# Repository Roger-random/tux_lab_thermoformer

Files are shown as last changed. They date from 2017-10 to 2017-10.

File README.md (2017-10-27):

# Tux-Lab Thermoforming Machine project

Files related to getting the Tux-Lab thermoforming machine back up and running.

## controls/AcrylicRelayPanel

Files for laser-cutting the relay panel and the toggle switches panel

## pi_touch_ui

The initial goal is to get the machine up and running with manual toggle switches. But being the tinkerer type - we know we will want to do more. This respository starts with an effort to create a machine control UI with PyQt5. The idea is to mount a Raspberry Pi the machine and control the machine this way.

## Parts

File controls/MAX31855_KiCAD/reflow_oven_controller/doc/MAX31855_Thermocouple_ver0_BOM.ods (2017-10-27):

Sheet: cc3300 V1
cc3000 WiFi Module
 |  |  |  |  |  |  |  |  | Buy
Quantity | Component | Part | Vendor | Vendor Item Number | Manufacturer | Manuf Part No. | Note | Cost | Qty | Price | Ext Price | Link
1 | C1 | 2.2pF 0603 | Digikey | 445-5617-1-ND | TDK | CGA3E2C0G1H2R2C080AA | CAP CER 2.2PF 50V NP0 0603 | 0.1 | 100 | 0.033 | 3.300 | http://www.digikey.com/product-detail/en/CGA3E2C0G1H2R2C080AA/445-5617-1-ND/2443657
1 | C2 | 10pF 0603 | Digikey | 445-1269-1-ND | TDK | C1608C0G1H100D080AA | CAP CER 10PF 50V NP0 0603 | 0.1 | 100 | 0.017 | 1.650 | http://www.digikey.com/product-detail/en/C1608C0G1H100D080AA/445-1269-1-ND/567671
1 | C3 | 1uF 0603 | Digikey
1 | C4 | 1uF 0603 | Digikey
1 | L1 | n/a | Digikey
1 | L2 | 2.2nH 0603 | Digikey | 712-1427-1-ND | Johnson Tech | L-14C2N2SV4T | CER INDUCTOR 2.2NH 0603 | 0.10 | 50 | 0.046 | 2.320 | http://www.digikey.com/product-detail/en/L-14C2N2SV4T/712-1427-1-ND/1914877
1 | U1 | TI cc3000 wifi | Digikey | 296-35057-ND | TI | CC3000MOD | MOD SIMPLELINK WI-FI CC300 | 14.49 | 3 | 14.490 | 43.470 | http://www.digikey.com/product-detail/en/CC3000MOD/296-35057-ND/3725883
1 | U2 | 74HC4050 | Digikey | 296-9215-1-ND | TI | CD74HC4050PWR | IC BUFFER HEX 1INPUT 16TSSOP | 0.49 | 10 | 0.412 | 4.120 | http://www.digikey.com/product-detail/en/CD74HC4050PWR/296-9215-1-ND/376723
1 | K1 | 3 pin header | Digikey
1 | K2 | 3 pin header | Digikey
1 | P1 | 7 pin header | Digikey
1 | Antenna | Antenna for FCC comp | Digikey | 712-1403-1-ND | Johnson Tech | 2500AT44M0400E | ANTENNA CHIP UWB 2.3 - 2.7 GHZ | 1.35 | 10 | 1.128 | 11.280 | http://www.digikey.com/product-detail/en/2500AT44M0400E/712-1403-1-ND/1840081
 |  |  |  |  |  |  | Component Cost: | 15.28 |  | 14.998 | 54.860

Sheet: MPL3115A2
MPL3115A2 WiFi Module
 |  |  |  |  |  |  |  |  | Buy
Quantity | Component | Part | Vendor | Vendor Item Number | Manufacturer | Manuf Part No. | Note | Cost | Qty | Price | Ext Price | Link
1* | C1 | 100nF | Digikey | 399-1095-1-ND | Kemet | C0603C104K8RACTU | 10V instead of 6.3V | 0.1 | 250 | 0.00944 |  | http://www.digikey.com/product-detail/en/C0603C104K8RACTU/399-1095-1-ND/411370
1* | C2 | 10uF | Digikey | 445-9104-1-ND | TDK | C1608X7S0J106M080AC | CAP CER 10UF 6.3V 20% X7S 0603 | 0.53 | 10 | 0.503 |  | http://www.digikey.com/product-detail/en/C1608X7S0J106M080AC/445-9104-1-ND/3661624
1* | C3 | 100nF | Digikey | 399-1095-1-ND | Kemet | C0603C104K8RACTU | 10V instead of 6.3V | 0.1 | 250 | 0.00944 |  | http://www.digikey.com/product-detail/en/C0603C104K8RACTU/399-1095-1-ND/411370
1* | C4 | .1uF | Digikey | 445-1314-1-ND | TDK | C1608X7R1H104K080AA | CAP CER 0.1UF 50V 10% X7R 0603 | 0.1 | 250 | 0.018 |  | http://www.digikey.com/product-detail/en/C1608X7R1H104K080AA/445-1314-1-ND/567687
1 | Q1 | BSS138 | Digikey | BSS138CT-ND | Fairchild | BSS138 | MOSFET N-CH 50V 220MA SOT-23 | 0.22 | 25 | 0.141 | 3.520 | http://www.digikey.com/product-detail/en/BSS138/BSS138CT-ND/244294
1 | Q2 | BSS138 | Digikey | BSS138CT-ND | Fairchild | BSS138 | MOSFET N-CH 50V 220MA SOT-23 | 0.22 | 25 | 0.141 | 3.520 | http://www.digikey.com/product-detail/en/BSS138/BSS138CT-ND/244294
1* | R1 | 10K | Digikey | MCT0603-10.0K-CFCT-ND | Vishay | MCT06030C1002FP500 | RES 10.0K OHM 1/8W 1% SMD 0603 | 0.08 | 100 | 0.0408 |  | http://www.digikey.com/product-detail/en/MCT06030C1002FP500/MCT0603-10.0K-CFCT-ND/2607933
1* | R2 | 10K | Digikey | MCT0603-10.0K-CFCT-ND | Vishay | MCT06030C1002FP500 | RES 10.0K OHM 1/8W 1% SMD 0603 | 0.08 | 100 | 0.0408 |  | http://www.digikey.com/product-detail/en/MCT06030C1002FP500/MCT0603-10.0K-CFCT-ND/2607933
1* | R3 | 10K | Digikey | MCT0603-10.0K-CFCT-ND | Vishay | MCT06030C1002FP500 | RES 10.0K OHM 1/8W 1% SMD 0603 | 0.08 | 100 | 0.0408 |  | http://www.digikey.com/product-detail/en/MCT06030C1002FP500/MCT0603-10.0K-CFCT-ND/2607933
1* | R4 | 10K | Digikey | MCT0603-10.0K-CFCT-ND | Vishay | MCT06030C1002FP500 | RES 10.0K OHM 1/8W 1% SMD 0603 | 0.08 | 100 | 0.0408 |  | http://www.digikey.com/product-detail/en/MCT06030C1002FP500/MCT0603-10.0K-CFCT-ND/2607933
1 | P1 | 7 Pin Header | Digikey
1 | U1 | MPL3115A2 | Digikey | MPL3115A2-ND | Freescale | MPL3115A2 | IC ALTIMETER I2C VERSION 8LGA | 2.88 | 5 | 2.720 | 13.600 | http://www.digikey.com/product-detail/en/MPL3115A2/MPL3115A2-ND/2817529
 |  |  |  |  |  |  | Component Cost: | 1.59 |  | 3.705 | 20.640
1* | L6470_v1
 | For version 2, go with 0805 C2 to lower cost
 | C2 | 10uF | Digikey | 587-2396-1-ND | Taiyo Yuden | JMK212B7106KG-T | CAP CER 10UF 6.3V 10% X7R 0805 | 0.27 | 50 | 0.111 |  | http://www.digikey.com/product-detail/en/JMK212B7106KG-T/587-2396-1-ND/2179009

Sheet: Si7021
 | MAX31855 Thermocouple Amplifier
 |  |  |  |  |  |  |  |  |  | Buy
 | Quantity | Component | Part | Vendor | Vendor Item Number | Manufacturer | Manuf Part No. | Note | Cost | Qty | Price | Ext Price | Link
 | 4 | C1, C2, C4, C5 | n/a
 | 4 | C3, C6 | .01uF +/-10% 16V X7R 0603 | Digikey | 478-6208-1-ND | AVX Corp | 0603YC103JAT2A | CAP CER 10000PF 16V 5% X7R 0603 | 0.15 | 100 | 0.048 | 4.75 | http://www.digikey.com/product-detail/en/0603YC103JAT2A/478-6208-1-ND/2391407
* | 2 | C7, C8, C9, C10 | 0.1uF +/-10%, 16V X7R 0603 | Digikey | 445-1314-1-ND | TDK | C1608X7R1H104K080AA | CAP CER 0.1UF 50V 10% X7R 0603 | 0.10 | 250 | 0.018 | 4.50 | http://www.digikey.com/product-detail/en/C1608X7R1H104K080AA/445-1314-1-ND/567687
 | 4 | R1, R2, R3, R4 | 150 Ohm +/-5% resistors (0603) | Digikey | MCT0603-150-CFCT-ND | Vishay Beyschlag | MCT06030C1500FP500 | RES 150 OHM 1/8W 1% SMD 0603 | 0.08 | 100 | 0.0408 | 4.08 | http://www.digikey.com/product-detail/en/MCT06030C1500FP500/MCT0603-150-CFCT-ND/2607884
 | 4 | FB1, FB2, FB3, FB4 | 470I ferrite beads (0603) | Digikey | 490-5223-1-ND | Murata | BLM18PG471SN1D | FERRITE CHIP 470 OHM 1000MA 0603 | 0.10 | 100 | 0.0501 | 5.01 | http://www.digikey.com/product-detail/en/BLM18PG471SN1D/490-5223-1-ND/1948399
 | 2 | U1, U2 | TVS diode NUP2105TL1G | Digikey | NUP2105LT1GOSCT-ND | On Semi | NUP2105LT1G | TVS DIODE 24VWM 44VC SOT23 | 0.44 | 10 | 0.37 | 3.71 | http://www.digikey.com/product-detail/en/NUP2105LT1G/NUP2105LT1GOSCT-ND/1485001
 | 2 | Alt U3, U4 | MAX31855KASA+ | Digikey | MAX31855KASA+TCT-ND | Maxim | MAX31855KASA+T | IC CONV THERMOCOUPLE-DGTL 8SOIC | 7.19 | 5 | 7.190 | 35.95 | http://www.digikey.com/product-detail/en/MAX31855KASA%2BT/MAX31855KASA%2BTCT-ND/2708805
 | 1 | U5 | TXB0104 Bidirection Shifter | Digikey | 296-21929-1-ND | TI | TXB0104PWR | IC VOLT-LEVEL TRANSLATOR 14TSSOP | 1.69 | 10 | 1.493 | 14.93 | http://www.digikey.com/product-detail/en/TXB0104PWR/296-21929-1-ND/1629282
** | 2 | P1, P2 | 3.5mm Tblock | Digikey | ED2635-ND | OnShore | OSTTE020161 | TERM BLOCK 3.5MM VERT 2POS PCB | 0.44 | 50 | 0.306 | 15.30 | http://www.digikey.com/product-search/en?vendor=0&keywords=ED2635-ND
 | 1 | P3 | Angle Header | Digikey | WM50026-35-ND | Molex | 22288353 | CONN HEADER 35POS .100 R/A GOLD | 2.07 | 10 | 1.853 | 18.53 | http://www.digikey.com/product-detail/en/0022288353/WM50026-35-ND/314240
 |  |  |  |  |  |  |  | Component Cost: | 19.833 |  | 18.249 | 106.760
 | * | L6470, C10, C11, C12, C13
 | **
 | Digikey Out of Stock – ETA 9/29/14
 | 2 | U3, U4 | MAX31855KASA+ | Digikey | MAX31855KASA+TCT-ND | Maxim | MAX31855KASA+-ND | IC CONV THERMOCOUPLE-DGTL SOIC | 4.50 | 10 | 4.275 | 42.75 | http://www.digikey.com/product-detail/en/MAX31855KASA%2BT/MAX31855KASA%2BTCT-ND/2708805

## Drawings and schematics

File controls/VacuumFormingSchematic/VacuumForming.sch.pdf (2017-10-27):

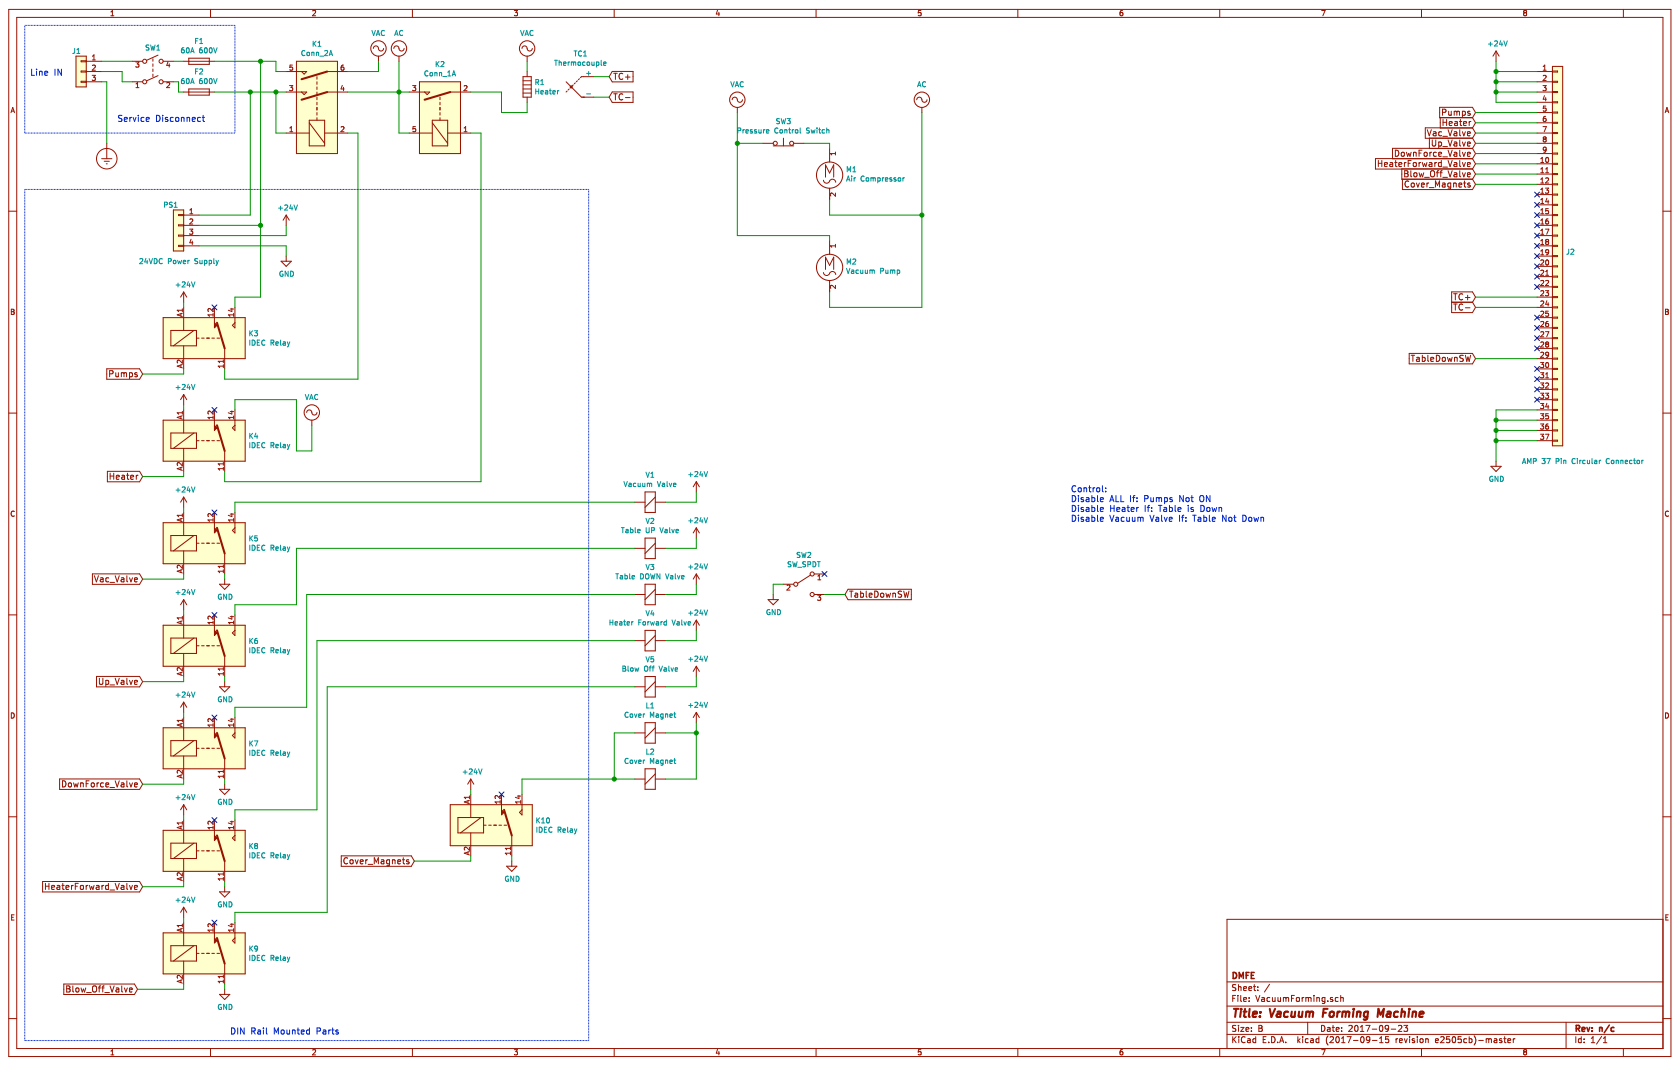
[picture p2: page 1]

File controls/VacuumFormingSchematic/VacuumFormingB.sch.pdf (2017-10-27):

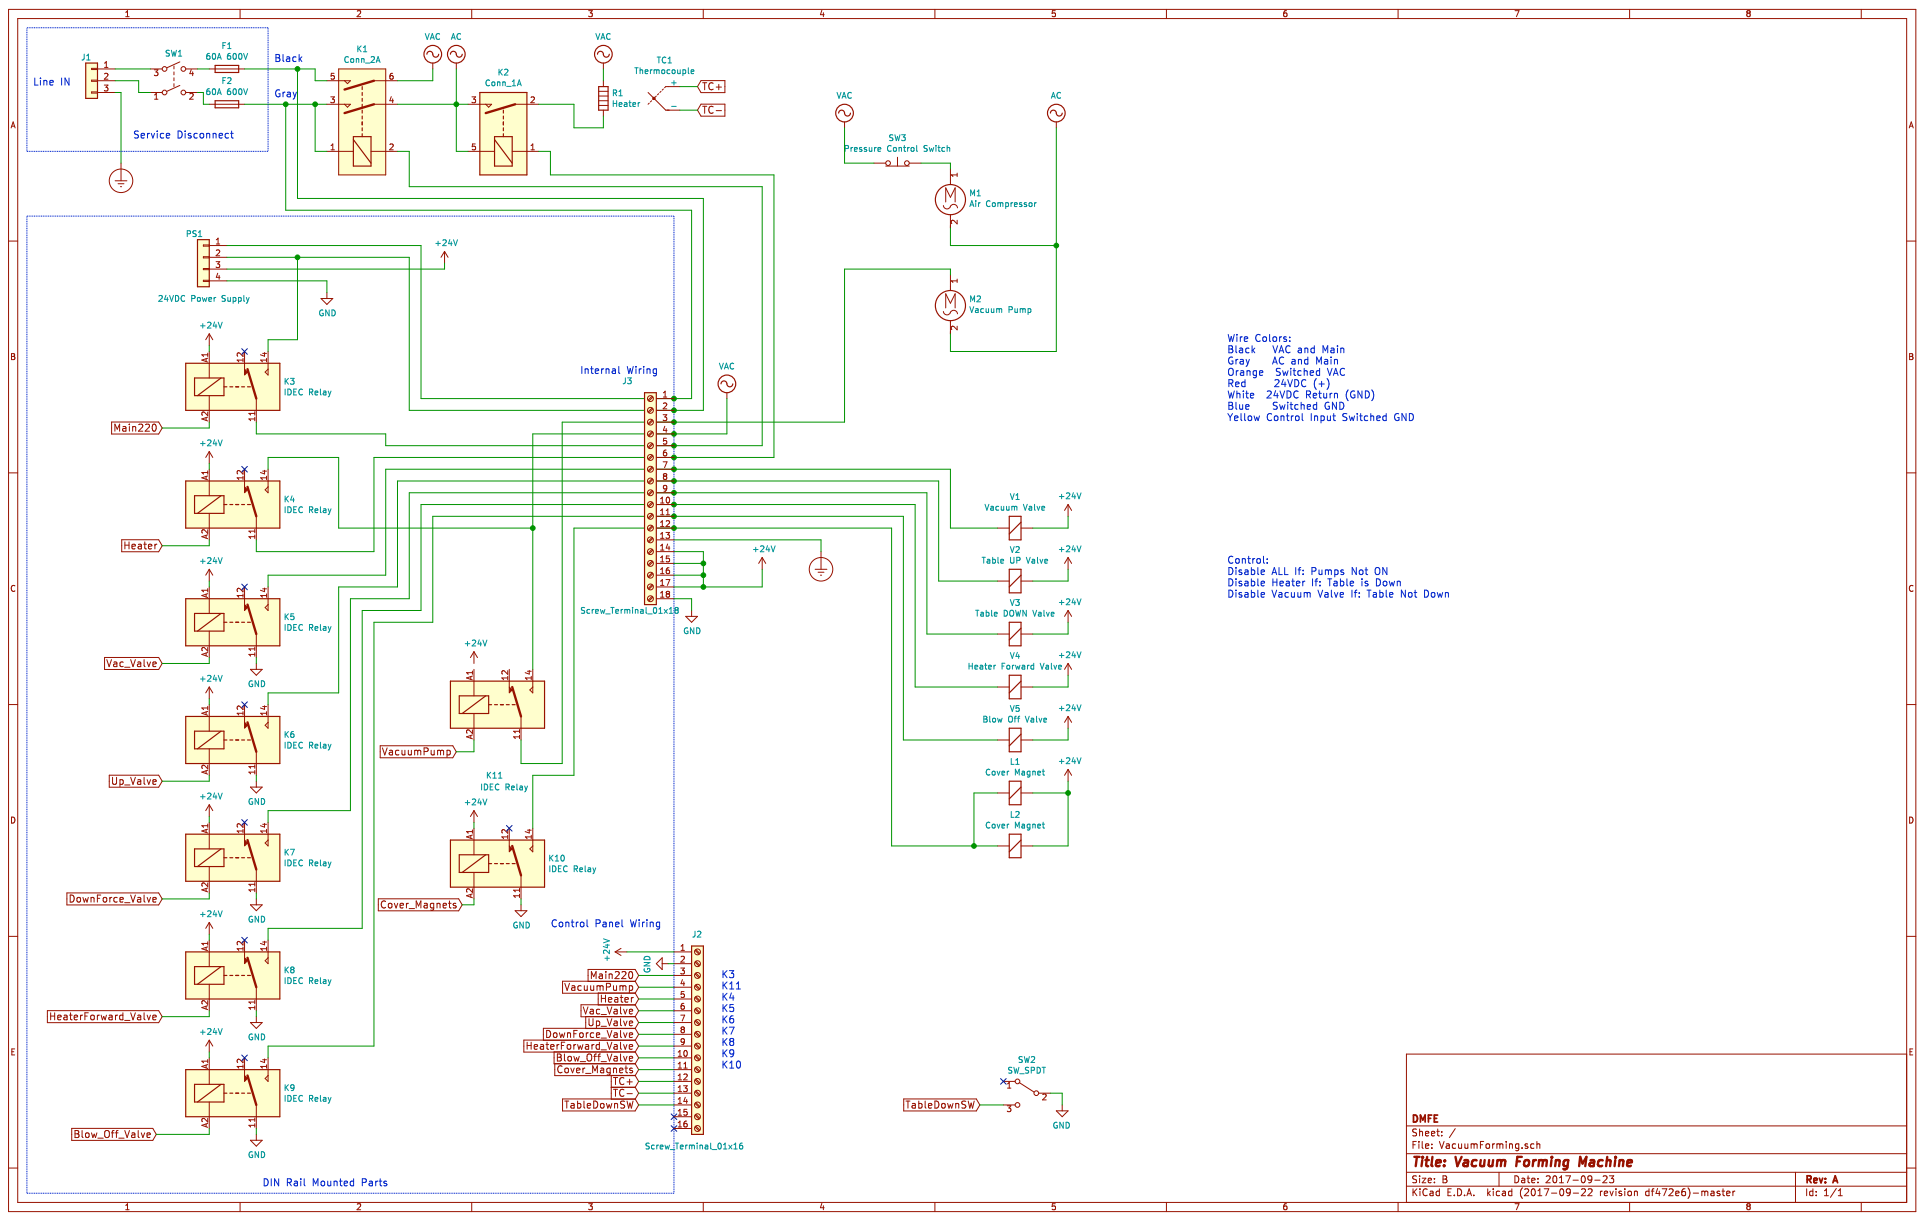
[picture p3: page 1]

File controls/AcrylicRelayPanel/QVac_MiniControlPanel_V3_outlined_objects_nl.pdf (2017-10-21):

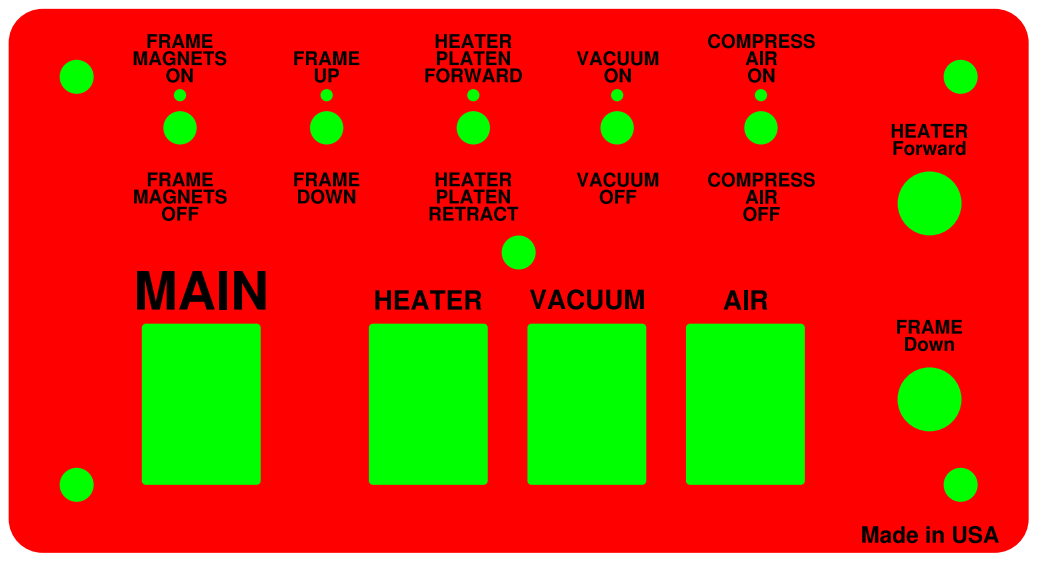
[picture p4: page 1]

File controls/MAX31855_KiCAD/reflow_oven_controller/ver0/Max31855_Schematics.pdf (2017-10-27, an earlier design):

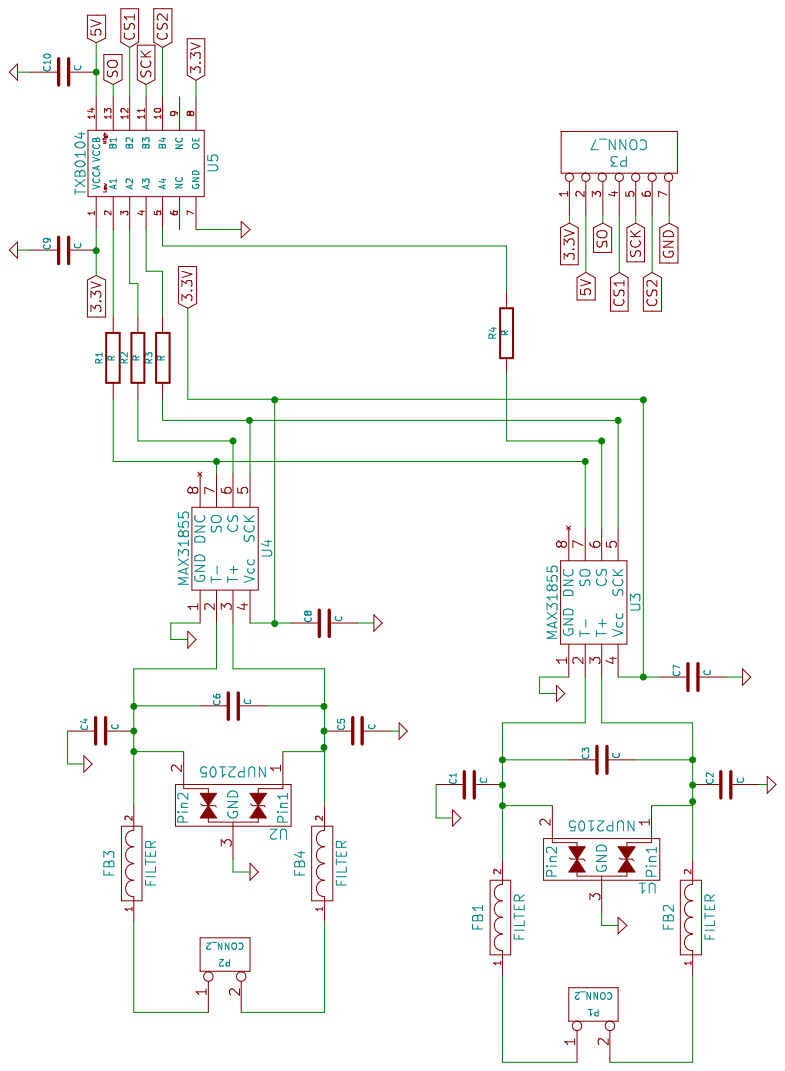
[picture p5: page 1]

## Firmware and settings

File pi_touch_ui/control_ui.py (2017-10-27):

import sys
import threading
from PyQt5.QtCore import QState, QStateMachine, Qt, QObject, pyqtSignal
from PyQt5.QtWidgets import QApplication, QMainWindow, QGridLayout, QGroupBox, QHBoxLayout, QVBoxLayout, QSizePolicy, QPushButton, QLabel, QWidget

try:
  import pigpio
except ImportError:
  import pigpio_stub as pigpio

#######################################################################
#
# Define constants
#
#######################################################################

#######################################################################
#
# Names here correspond to labels on the schematic

# Relay control
main220 = "Main220"
vacuumpump = "VacuumPump"
heater = "Heater"
vacvalve = "Vac_Valve"
upvalve = "Up_Valve"
downforcevalve = "DownForce_Valve"
heaterforwardvalve = "HeaterForward_Valve"
blowoffvalve = "Blow_Off_Valve"
covermagnets = "Cover_Magnets"

# Status switches
tabledownsw = "TableDownSW"

#######################################################################
#
# Map the schematic names to GPIO pins.

digitalInputs = {
  tabledownsw: 5
}

digitalOutputs = {
  main220 : 19,
  vacuumpump : 27,
  heater : 13,
  vacvalve : 22,
  upvalve : 26,
  downforcevalve : 21,
  heaterforwardvalve : 20,
  blowoffvalve : 16,
  covermagnets : 12
}

#######################################################################
#
# The states of the above I/O are shown to the user on the status bar
# of the main window. This list describes how they are shown in the
# status bar. The items are organized roughly in the order they are
# expected to activate in normal operation.
# * First entry is the label to use in the status bar.
# * Second entry is the name of the input or output. When this is an
#   empty string, the first entry is just a label used to categorize 
#   the I/O that follows it. It has no direct mapping to an I/O port 
#   itself.

statusIO = (
  ("Power", ""),
  ("220V", main220),
  ("Vacuum", vacuumpump),
  ("Heater", ""),   # 'Heater' here is a category label.
  ("On", heater),
  ("Forward", heaterforwardvalve),
  ("Frame", ""),
  ("Up", upvalve),
  ("Magnet", covermagnets),
  ("Drop", tabledownsw),
  ("Down", downforcevalve),
  ("Table", ""),
  ("Vacuum", vacvalve),
  ("Air", blowoffvalve)
)

#######################################################################
#
# Style sheets

ioOnStyle = "* { font-size:18px; background-color : green; color : white }"
ioOffStyle = "* { font-size:18px; background-color : white; color : gray }"
stateStyle = "* { font:bold; font-size:24px }"
readableTextStyle = "* { font-size:20px }"

#######################################################################
#
# Time-related constants

debounceWaitPeriod = 0.2 # Seconds to wait for GPIO level to settle.

#######################################################################
#
# Utility classes
#
#######################################################################

# DelayedCall
#
# Similar to Qt's QTimer::singleShot(), but does not require caller to
# have launched with QThread. We use Python's threading.Timer instead.
#
# Note: QTimer::singleShot() takes delay in milliseconds, Python
# threading.Timer takes delay in seconds and that's what we use here.

class DelayedCall(QObject):

  uiThreadSignal = pyqtSignal()

  def __init__(self, delay, callback, parent=None):
    super().__init__(parent)
    self.uiThreadSignal.connect(callback, Qt.QueuedConnection)
    threading.Timer(delay, self.timerThreadCallback).start()

  def timerThreadCallback(self):
    self.uiThreadSignal.emit()

#######################################################################
#
# Custom UI elements derived from standard Qt UI
#
#######################################################################

#######################################################################
#
# CenteredLabel puts QLabel text in the center and makes it larger for
# readability. TODO: make this class unnecessary with use of an app-
# wide stylesheet.

class CenteredLabel(QLabel):

  def __init__(self, text=None, parent=None):
    super().__init__(text, parent)
    self.setAlignment(Qt.AlignCenter)
    self.setStyleSheet(readableTextStyle)

#######################################################################
#
# GPIOLabel is a label that changes its visual appearance (but maintain
# the same text) corresponding to the state of its corresponding
# GPIO pin.

class GPIOLabel(QLabel):

  def __init__(self, name, gpioControl, pin, parent=None):
    super().__init__(name, parent)
    self.gpioControl = gpioControl
    self.gpioPin = pin
    self.pinState = self.gpioControl.read(self.gpioPin)
    self.updateStyle()
    self.debounceWaiting = False
    gpioControl.callback(pin, pigpio.EITHER_EDGE, self.levelChangeCallback)

  def levelChangeCallback(self, gpio, level, tick):
    if gpio == self.gpioPin:
      if not self.debounceWaiting:
        self.debounceWaiting = True
        self.debounceDelay = DelayedCall(debounceWaitPeriod, self.waitedDebouncePeriod)

  def waitedDebouncePeriod(self):
    currentState = self.gpioControl.read(self.gpioPin)
    if currentState != self.pinState:
      self.pinState = currentState
      self.updateStyle()
    self.debounceWaiting = False

  def updateStyle(self):
    if self.pinState:
      self.setStyleSheet(ioOnStyle)
    else:
      self.setStyleSheet(ioOffStyle)

#######################################################################
#
# StateLabel is used at the top of the screen to indicate the current
# state of the control

class StateLabel(QLabel):
  def __init__(self, name, parent=None):
    super().__init__(name.upper(), parent)
    self.setAlignment(Qt.AlignCenter)
    self.setStyleSheet(stateStyle)

#######################################################################
#
# Default QPushButton expands horizontally to fill available space but
# only take up as much vertical space as it needs for the enclosed label.
# This derived class expands to fill both horizontally and vertically.

class ExpandButton(QPushButton):
  def __init__(self, text, parent=None):
    super().__init__(text, parent)
    self.setSizePolicy(QSizePolicy.Expanding, QSizePolicy.Expanding)
    self.setStyleSheet(readableTextStyle)

#######################################################################
#
# This button is modified to have an on/off state (checked true/false)
# that is toggled on each press.

class ExpandToggleButton(ExpandButton):
  def __init__(self, text, name, parent=None):
    super().__init__(text, parent)
    self.setCheckable(True)
    self.updateCheckedStyle()
    self.pinName = name

  def updateCheckedStyle(self):
    if self.isChecked():
      self.setStyleSheet(ioOnStyle)
    else:
      self.setStyleSheet(ioOffStyle)

  def nextCheckState(self):
    super().nextCheckState()
    self.updateCheckedStyle()

#######################################################################
#
# The top navigation bar consists of a grid layout with four equal-
# sized positions.
#  Leftmost: (Column 0) should be a button that takes user "back"
#  Rightmost:(Column 3) should be a button that takes user "forward"
#  Middle two (Column 1 and 2) can vary depending on state.
#
# TODO: is this better accomplished with a QToolbar?

class NavBar(QGridLayout):
  def __init__(self, parent=None):
    super().__init__(parent)
    self.setColumnStretch(0, 1)
    self.setColumnStretch(1, 1)
    self.setColumnStretch(2, 1)
    self.setColumnStretch(3, 1)

  def addNav(self, navItem, column):
    self.addWidget(navItem, 0, column)

#######################################################################
#
# StateUI is the template for a QWidget that holds all the UI for a state

class StateUI(QWidget):
  def __init__(self, navbar, label, controls, parent=None):
    super().__init__(parent)
    vbox = QVBoxLayout()
    vbox.insertLayout(-1, navbar, stretch=2)
    vbox.addWidget(StateLabel(label), stretch=1)
    vbox.insertLayout(-1, controls, stretch=9)
    self.setLayout(vbox)

#######################################################################
#
# PlaceholderLayout is a grid layout with a single QLabel with the given
# text. (Text-wrapping is activated.)

class PlaceholderLayout(QGridLayout):
  def __init__(self, label, parent=None):
    super().__init__(parent)
    l = QLabel(label)
    l.setWordWrap(True)
    self.addWidget(l)

#######################################################################
#
# Application UI
#
#######################################################################
    
#######################################################################
#
# Main Window class is the master of all UI on screen.

class MainWindow(QMainWindow):

  # Initialization
  def __init__(self, gpioControl, parent=None):
    super().__init__(parent)
    self.createStatusIO(gpioControl)
    self.setGeometry(0, 0, 800, 480)
    self.setWindowTitle("Tux Lab Thermoforming Control")
    self.show() # Will need to be showFullScreen() on the Pi touchscreen.

  # Walks through the statusIO list and create either an OnOffLabel
  # (For those with a label listed in digitalInputs or digitalOutputs
  # array) or a normal QLabel (For those without.)
  def createStatusIO(self, gpioControl):
    for sio in statusIO:
      if sio[1] in digitalInputs:
        ioLabel = GPIOLabel(sio[0], gpioControl, digitalInputs[sio[1]])
      elif sio[1] in digitalOutputs:
        ioLabel = GPIOLabel(sio[0], gpioControl, digitalOutputs[sio[1]])
      else:
        ioLabel = QLabel(sio[0])
      self.statusBar().addPermanentWidget(ioLabel)
    
#######################################################################
#
# I/O Management
#
#######################################################################

class IOManager(QObject):

  def __init__(self, uiOwner, gpioControl, parent=None):
    super().__init__(parent)
    self.uiOwner = uiOwner
    self.pi = gpioControl
    if not self.pi.connected:
      print("Pi I/O is not connected")
    for pin in digitalInputs.values():
      self.pi.set_mode(pin, pigpio.INPUT)
    for pin in digitalOutputs.values():
      self.pi.set_mode(pin, pigpio.OUTPUT)
    self.outputReset()

  def prepExit(self):
    self.pi.stop()

  def outputReset(self):
    for doName in digitalOutputs.keys():
      self.turnOff(doName)

  def expandToggleChanged(self, event):
    expandToggle = self.sender()
    name = expandToggle.pinName
    if event:
      self.turnOn(name)
    else:
      self.turnOff(name)

  def turnOn(self, name):
    gpio = digitalOutputs[name]
    self.pi.write(gpio, 1)

  def turnOff(self, name):
    gpio = digitalOutputs[name]
    self.pi.write(gpio, 0)

  def isOn(self, name):
    return self.pi.read(digitalOutputs[name])

#######################################################################
#
# Application States & State Machine
#
#######################################################################

#######################################################################
#
# MachineState is the base class for all states in this machine.
class MachineState(QState):
  def __init__(self, uiWindow, ioManager, parent=None):
    super().__init__(parent)
    self.uiWindow = uiWindow
    self.ioManager = ioManager
    self.setupUI()

  def setupUI(self):
    self.ui = QLabel("Default MachineState UI needs to be overridden")

  def onEntry(self, event):
    self.uiWindow.setCentralWidget(self.ui)

  def onExit(self, event):
    # Reclaim the 'self.ui' object so uiWindow doesn't delete it
    self.uiWindow.takeCentralWidget()
    
#######################################################################
#
# StandByState is the initial start-up state

class StandbyState(MachineState):

  # Set up the UI to be shown for this state
  def setupUI(self):
    self.btnDC = ExpandButton("< Direct Control")
    self.btnStartup = ExpandButton("Startup >")
    
    navBar = NavBar()
    navBar.addNav(self.btnDC, 0)
    navBar.addNav(self.btnStartup, 3)

    standbyMenu = QGridLayout()
    standbyMenu.addWidget(ExpandButton("TODO: Hold to shut down"))
    
    self.ui = StateUI(navBar, "standby", standbyMenu)

  def onEntry(self, e):
    super().onEntry(e)
    self.ioManager.outputReset()

  # Called by state machine to connect transitions
  def toDirectControl(self, directControl):
    self.addTransition(self.btnDC.clicked, directControl)
    
  def toStartup(self, startupState):
    self.addTransition(self.btnStartup.clicked, startupState)

#######################################################################
#
# DirectControlState allows direct access to outputs

class DirectControlState(MachineState):

  # Set up the UI to be shown for this state
  def setupUI(self):
    self.btnSB = ExpandButton("Standby >")
    navBar = NavBar()
    navBar.addNav(self.btnSB, 3)
    
    self.controlButtons = dict()
    controlMenu = QHBoxLayout()
    for sio in statusIO:
      if sio[1] == "":
        groupBox = QGroupBox(sio[0])
        groupBoxLayout = QVBoxLayout()
        groupBox.setLayout(groupBoxLayout)
        controlMenu.addWidget(groupBox)
      elif sio[1] in digitalOutputs:
        btn = ExpandToggleButton(sio[0], sio[1])
        btn.clicked.connect(self.ioManager.expandToggleChanged)
        groupBoxLayout.addWidget(btn)
        self.controlButtons[sio[1]] = btn
      elif sio[1] in digitalInputs:
        continue
      else:
        print("Warning: Extraneous element in statusIO. Was there a misspelling? " + sio[1])
    
    self.ui = StateUI(navBar, "direct control", controlMenu)

  def onEntry(self, e):
    super().onEntry(e)
    for k,v in self.controlButtons.items():
      v.setChecked(self.ioManager.isOn(k))
      v.updateCheckedStyle()

  def toStandby(self, standby):
    self.addTransition(self.btnSB.clicked, standby)

#######################################################################
#
# StartupState turns all the main components on in preparation for loading

class StartupState(MachineState):
  def setupUI(self):
    self.btnStandby = ExpandButton("< Standby")
    self.btnLoading = ExpandButton("Load >")
    navBar = NavBar()
    navBar.addNav(self.btnStandby, 0)
    navBar.addNav(self.btnLoading, 3)
    
    self.mainPowerLabel = CenteredLabel()
    self.vacuumPowerLabel = CenteredLabel()
    self.heaterPowerLabel = CenteredLabel()
    self.waitForLoad = CenteredLabel()
    
    startupLabels = QVBoxLayout()
    startupLabels.addWidget(QLabel()) # Spacer
    startupLabels.addWidget(self.mainPowerLabel)
    startupLabels.addWidget(self.vacuumPowerLabel)
    startupLabels.addWidget(self.heaterPowerLabel)
    startupLabels.addWidget(self.waitForLoad)
    startupLabels.addWidget(QLabel()) # Spacer

    self.ui = StateUI(navBar, "starting up", startupLabels)
    
  def toStandby(self, standby):
    self.addTransition(self.btnStandby.clicked, standby)

  def toLoading(self, loading):
    self.addTransition(self.btnLoading.clicked, loading)
    
  def onEntry(self, event):
    super().onEntry(event)
    self.btnLoading.setEnabled(False) # Wait until everything turns on before enabling.
    self.ioManager.turnOn(main220)
    self.mainPowerLabel.setText("Main 220V Power: ON")
    self.vacuumPowerLabel.setText("Vacuum Pump Power: (Waiting)")
    self.heaterPowerLabel.setText("Heater Power: (Waiting)")
    self.waitForLoad.setText("")
    self.delayedCall = DelayedCall(2, self.turnOnVacuum)

  def turnOnVacuum(self):
    self.ioManager.turnOn(vacuumpump)
    self.vacuumPowerLabel.setText("Vacuum Pump Power:  ON")
    self.delayedCall = DelayedCall(2, self.turnOnHeater)

  def turnOnHeater(self):
    self.ioManager.turnOn(heater)
    self.heaterPowerLabel.setText("Heater Power:  ON")
    self.waitForLoad.setText("Startup Complete: Press Load to Begin")
    self.btnLoading.setEnabled(True) # Enable button to proceed to Loading

#######################################################################
#
# Loading state raises the frame so operator can load work material

class LoadingState(MachineState):
  def setupUI(self):
    self.btnStandby = ExpandButton("< Standby")
    self.btnHeating = ExpandButton("Heat >")
    navBar = NavBar()
    navBar.addNav(self.btnStandby, 0)
    navBar.addNav(self.btnHeating, 3)

    loadingMenu = PlaceholderLayout("TODO: (1) Button to start auto-cycle. (2) Button to allow operator to raise/lower the frame as needed. (3) Button to turn magnet on/off (4) Deactivate forward progress until heater is up to temperature")

    self.ui = StateUI(navBar, "loading", loadingMenu)

  def toStandby(self, standby):
    self.addTransition(self.btnStandby.clicked, standby)

  def toHeating(self, heating):
    self.addTransition(self.btnHeating.clicked, heating)

  def onEntry(self, event):
    super().onEntry(event)
    self.ioManager.turnOn(heater)
    self.ioManager.turnOn(upvalve)
    self.ioManager.turnOn(covermagnets)

  def onExit(self, e):
    super().onExit(e)

#######################################################################
#
# Heating state holds the workpiece up to the heater

class HeatingState(MachineState):
  def setupUI(self):
    self.btnLoading = ExpandButton("< Load")
    self.btnDrop = ExpandButton("Drop >")
    navBar = NavBar()
    navBar.addNav(self.btnLoading, 0)
    navBar.addNav(self.btnDrop, 3)

    heatingMenu = PlaceholderLayout("TODO: Timer counts up on heating duration. Show time threshold parameter for auto operation. Option to turn off auto operation")

    self.ui = StateUI(navBar, "heating", heatingMenu)

  def toLoading(self, loading):
    self.addTransition(self.btnLoading.clicked, loading)

  def toDrop(self, drop):
    self.addTransition(self.btnDrop.clicked, drop)

  def onEntry(self, e):
    super().onEntry(e)
    self.ioManager.turnOn(heaterforwardvalve)

  def onExit(self, e):
    super().onExit(e)
    self.ioManager.turnOff(heaterforwardvalve)

#######################################################################
#
# Drop state waits for the frame to drop to the table

class DropState(MachineState):
  def setupUI(self):
    self.btnHeating = ExpandButton("< Heat")
    self.btnForming = ExpandButton("Form >")
    navBar = NavBar()
    navBar.addNav(self.btnHeating, 0)
    navBar.addNav(self.btnForming, 3)

    dropMenu = PlaceholderLayout("TODO: Button to active downforce instead of waiting. Timer to count how long we've waited for drop. Disable forward progress until frame down switch is closed.")

    self.ui = StateUI(navBar, "dropping", dropMenu)

  def toHeating(self, heating):
    self.addTransition(self.btnHeating.clicked, heating)

  def toForming(self, forming):
    self.addTransition(self.btnForming.clicked, forming)

  def onEntry(self, e):
    super().onEntry(e)
    self.ioManager.turnOff(heater)
    self.ioManager.turnOff(upvalve)

  def onExit(self, e):
    super().onExit(e)
    if e.sender() == self.btnHeating:
      self.ioManager.turnOn(heater)
      self.ioManager.turnOn(upvalve)

#######################################################################
#
# Forming state applies vacuum to pull workpiece against mold

class FormingState(MachineState):
  def setupUI(self):
    self.btnComplete = ExpandButton("Complete >")
    navBar = NavBar()
    navBar.addNav(self.btnComplete, 3)

    formingMenu = PlaceholderLayout("TODO: Timer to count how long we've been forming. Show timer threshold for auto cycle. Option to disable auto cycle.")

    self.ui = StateUI(navBar, "forming", formingMenu)

  def toComplete(self, complete):
    self.addTransition(self.btnComplete.clicked, complete)

  def onEntry(self, e):
    super().onEntry(e)
    self.ioManager.turnOn(downforcevalve)
    self.ioManager.turnOn(vacvalve)

  def onExit(self, e):
    super().onExit(e)
    self.ioManager.turnOff(downforcevalve)
    self.ioManager.turnOff(vacvalve)

#######################################################################
#
# Forming operating complete, operator can remove workpiece.

class CompleteState(MachineState):
  def setupUI(self):
    self.btnStandby = ExpandButton("< Standby")
    self.btnLoading = ExpandButton("Load >")
    navBar = NavBar()
    navBar.addNav(self.btnStandby, 0)
    navBar.addNav(self.btnLoading, 3)

    self.btnMagnet = ExpandToggleButton("Magnets", covermagnets)
    self.btnMagnet.setChecked(True)
    self.btnMagnet.updateCheckedStyle()
    self.btnMagnet.clicked.connect(self.ioManager.expandToggleChanged)

    self.btnBlowoff = ExpandToggleButton("Blowoff", blowoffvalve)
    self.btnBlowoff.setChecked(False)
    self.btnBlowoff.clicked.connect(self.ioManager.expandToggleChanged)

    completeMenu = QHBoxLayout()
    completeMenu.addWidget(self.btnMagnet, 1)
    completeMenu.addWidget(self.btnBlowoff, 1)

    self.ui = StateUI(navBar, "complete", completeMenu)

  def onEntry(self, e):
    super().onEntry(e)
    self.btnMagnet.setChecked(True) # TODO: Can this be read from IOManager?
    self.btnMagnet.updateCheckedStyle()

  def toStandby(self, standby):
    self.addTransition(self.btnStandby.clicked, standby)

  def toLoading(self, loading):
    self.addTransition(self.btnLoading.clicked, loading)

#######################################################################
#
# Main state machine of the thermoformer control
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

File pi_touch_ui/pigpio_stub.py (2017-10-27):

"""
This is a stub of the Raspberry Pi default Python GPIO library, just
barely enough to test this project on a non-Pi computer.

Reference the original at
http://abyz.me.uk/rpi/pigpio/python.html
https://github.com/joan2937/pigpio/blob/master/pigpio.py
"""

# GPIO edges

EITHER_EDGE  = 2

# GPIO modes

INPUT  = 0
OUTPUT = 1

def pi():
  return pigpio_stub()

class pigpio_stub(object):
  def __init__(self):
    super().__init__()
    print("pigpio_stub initialize")
    self.connected = True

  def callback(self, user_gpio, edge, func):
    print("Callback requested on pin ", str(user_gpio))

  def read(self, user_gpio):
    print("Attempted to read pin ", str(user_gpio))
    return 0;

  def set_mode(self, gpio, mode):
    print("Setting mode of pin ", str(gpio))

  def stop(self):
    print("Stop was called")

  def write(self, gpio, level):
    print("Writing to pin ", str(gpio))

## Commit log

2017-10-06 Keep CompleteState magnet button in sync on each run
2017-10-06 Pin 5 and 6 leaks power on startup, before any code runs. Do not use them for driving relays.
    [control_ui.py]
2017-10-07 Increase button label text size
2017-10-08 Use threading.Timer for debouncing pin level changes
2017-10-08 Remove debugging print() for debounce routine
2017-10-08 GPIOLabel finally does what its name says: reflect GPIO pin state in its visual style.
2017-10-08 Switch from OnOffLabel to GPIOLabel. Now the status labels are actually status of the pins as read from pigpiod. The IOManager is no longer responsible for manually switching them.
    [control_ui.py]
2017-10-09 DelayedCall for time-delayed callback on UI thread
2017-10-09 (1) ActiveState use DelayedCall to wait 2 seconds between turnOn. (2) DirectControlState tracks its buttons and synchronizes their states with the GPIO pin upon onEntry
2017-10-20 KiCAD relay board revised layout. Inkscape acrylic relay board.
    [QVac.kicad_pcb, QVac.sch]
2017-10-22 removed QVac_RelayPanel
    [QVac.kicad_pcb, QVac.sch]
2017-10-23 Move Raspberry Pi touchscreen project to subdirectory
2017-10-23 Remove Raspberry Pi touchscreen files from root directory of project
2017-10-26 Added Schematic
    [VacuumForming.kicad_pcb, VacuumForming.sch]
2017-10-27 added kicad files for MAX31855 TC amp board
    [Adafruit_MAX31855 v2.brd, Adafruit_MAX31855 v2.sch, Adafruit_MAX31855.brd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]
